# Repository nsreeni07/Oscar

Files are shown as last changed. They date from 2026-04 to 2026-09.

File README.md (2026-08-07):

OSCAR

Autonomous UAV system for precision agricultural crop monitoring

OSCAR is a custom-built 850mm quadcopter designed to fly automated survey missions over farmland and produce NDVI (Normalized Difference Vegetation Index) health maps of crops. It flies pre-programmed waypoint missions on INAV, captures geotagged near-infrared imagery, and a ground station does orthomosaic stitching and vegetation analysis. The end result is a color-coded map of a field showing where crops are healthy, where they're under irrigation stress, and where disease pressure might be building, all without a human piloting the aircraft or walking the field.

Onshape CAD: https://cad.onshape.com/documents/19523291b70a9c787e4fbec5/w/8af018b0ace6f9250dc6f3df/e/06f56f02d452d38e7c73aa30 
Full BOM: https://docs.google.com/spreadsheets/d/1ItluG4JZ7m0poAZtw0F7x5zs6U-Jy8w3EoTn_GnxS2I

How it works

OSCAR flies a field, takes pictures, and turns those pictures into a crop health map. Three steps:

Plan — a survey area is broken into a grid of GPS waypoints with enough overlap for the images to stitch together later. This mission gets loaded onto the flight controller in INAV Configurator.
Fly and capture — the drone flies the waypoints on its own. At each one, the flight controller tells the Pi Zero 2W over MAVLink that it's arrived. The Pi triggers the NIR camera  and geotags the image with the GPS position.
Process — after landing, the images go from the Pi's SD card to a ground station laptop running WebODM. WebODM stitches them into one map of the field and runs NDVI, which compares red vs. near-infrared reflectance to score plant health. Healthy plants reflect a lot of NIR, stressed or dying plants reflect more red. WebODM turns that into a color map, red for poor health, green for good, so problem spots in the field are obvious at a glance.







# Project OSCAR — Bill of Materials
|OSCAR — Updated Bill of Materials|FIELD2 |FIELD3|FIELD4 |FIELD5 |FIELD6 |FIELD7 |
|---|---|---|---|---|---|---|
| | | | | | | |
|Category |Item |Qty |Unit Price ($)|Line Total ($)|Notes |Link |
|Flight Controller / ESC |SpeedyBee F405 V4 BLS 60A 30x30 FC + 60A 4-in-1 ESC|1 |$70.31 |$70.31 |FC + ESC stack, replaces F722 + separate PDB/PM06 |https://tinyurl.com/2nz8ucyx |
|Companion Computer |Raspberry Pi Zero 2W |1 |$20.00 |$20.00 |Runs NDVI pipeline + MAVLink telemetry |https://www.adafruit.com/piz2w?src=raspberrypi |
|Camera |Pi Camera v2 NoIR |1 |$15.00 |$15.00 |Paired with 680nm bandpass filter for NDVI |https://www.pishop.us/product/raspberry-pi-noir-camera-module-v2/?src=raspberrypi|
|Power |XT90 Male-Female Pairs |1 |$3.00 |$3.00 |Battery-to-frame power connectors |https://tinyurl.com/m3hn7ykb |
|Power Protection |50V 2200µF Low-ESR Electrolytic Capacitor |1 |$3.00 |$3.00 |Across ESC battery pads — 6S voltage spike protection|https://tinyurl.com/yksjk3cu |
|Logistics |Shipping |1 |$35.00 |$35.00 |Combined shipping across vendors | |
| | | |Total |$146.31 | | 

Assembly

Build order, roughly in this sequence:

Frame — Cut the four CF tubes to 500mm. Press heat-set inserts into the 3D printed motor mount clamps, bolt clamps onto the tube ends. Assemble the central hub, routing motor and GPS/telemetry wiring through it before closing it up. Leave the FC/ESC deck plate off for now.

Propulsion — Bolt on the motors with threadlocker on every screw. Hold off on props until after ESC calibration. Two props are CW, two are CCW, check rotation direction against the SpeedyBee's motor order before mounting.

Power wiring — Solder the XT60 to the main 12 AWG battery leads, then wire the 4-in-1 ESC to the same leads. Solder the 2200uF capacitor across the ESC's battery pads for spike protection. Run 18 AWG phase wire from each motor through the arm tubes to its ESC output. Wire the two UBECs off the main power lead, one to the FC, one to the Pi, kept separate.
Flight controller — Mount the SpeedyBee F405 V4 stack on its vibration grommets near the frame's center of mass. Mount the GPS/compass on a mast, away from the ESC. Wire the SiK telemetry radio to a UART. Bind and wire the FlySky receiver to iBus.

Flash and configure INAV — Flash INAV to the SpeedyBee. Set the mixer to quad X, calibrate accelerometer and compass, confirm GPS lock, run ESC calibration with props off, set RC failsafe to RTL. Only mount props after confirming motor direction and throttle response in the motor test tab.

Payload — Confirm the IR-cut filter is removed from the NoIR camera, then thread on the 680nm bandpass filter. Connect the camera to the Pi Zero 2W via the CSI adapter. Mount the Pi and camera on the passive gimbal, mount the gimbal to the frame's underside. Power the Pi off its own UBEC rail.

Telemetry link and trigger logic — Wire a UART from the flight controller to the Pi so it can read the MAVLink stream. Run the waypoint-reached listener script from UAV Code/ on the Pi, which fires the camera and geotags on trigger. Bench-test this indoors before flying.

Balance and pre-flight check — Confirm the aircraft balances near center with the battery installed, arms are square, and motors spin freely. Run a full pre-flight (GPS lock, compass, RC link, telemetry link) and a hover test before attempting a waypoint mission.

Ground station — Install WebODM . After a flight, pull images off the Pi's SD card, load them into a WebODM project, and run the orthomosaic and NDVI task. Output is viewable in WebODM or exportable as a GeoTIFF.|

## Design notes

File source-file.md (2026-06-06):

https://cad.onshape.com/documents/ae291fcf005e21f8ead63777/w/105ae2836a2d5d7bdb4a4c74/e/ae3124f8bb89971ef9b9c9ca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

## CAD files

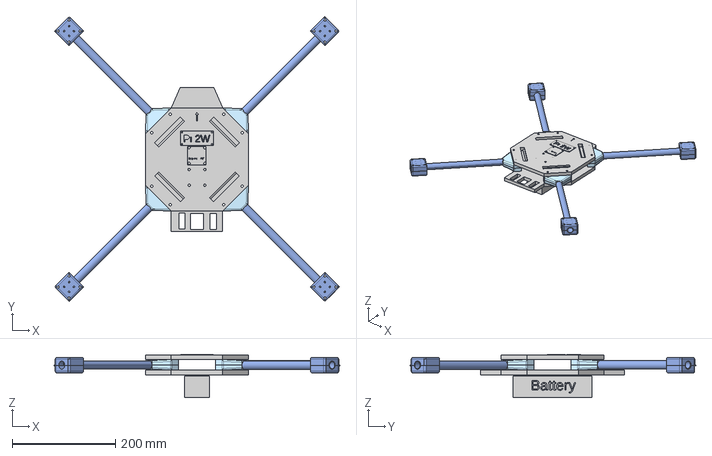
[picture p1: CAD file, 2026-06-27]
CAD Models/Oscar Drone Full Model with Electronics.step
553.1 x 553.1 x 83.9 mm

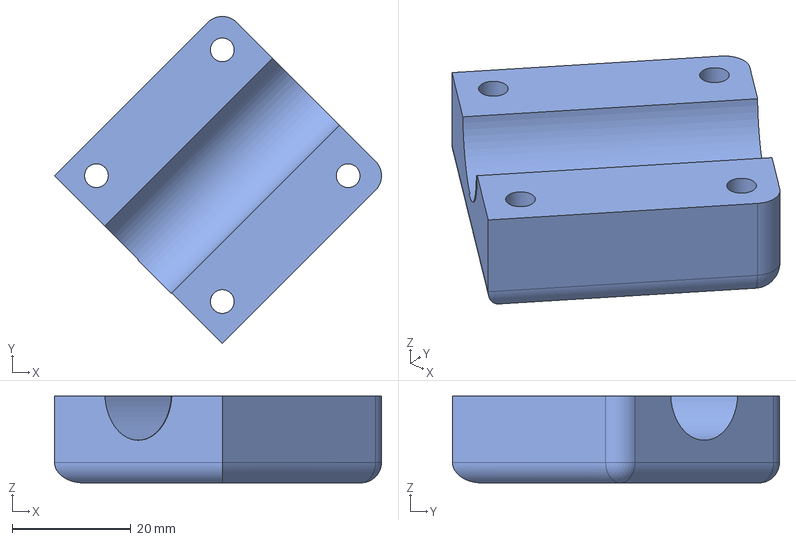
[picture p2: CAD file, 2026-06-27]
CAD Models/Part Studio 1 - Motor Mount Botto FR.step
55.1 x 55.1 x 14.7 mm

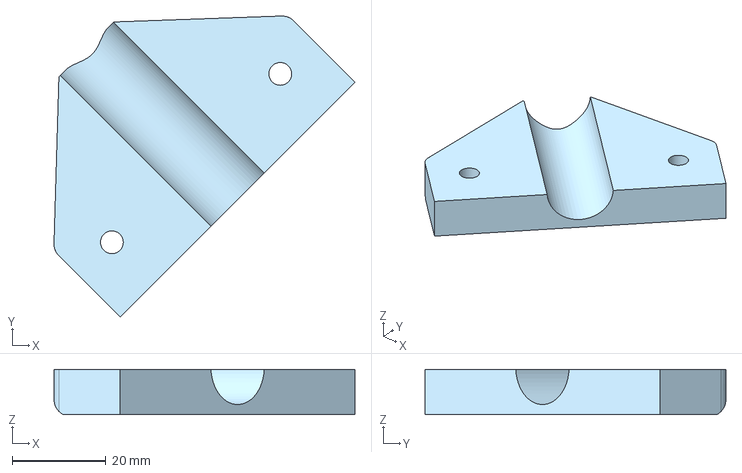
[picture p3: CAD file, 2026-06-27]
CAD Models/Part Studio 1 - Arm Mount FL 2.step
64.1 x 64.1 x 9.65 mm

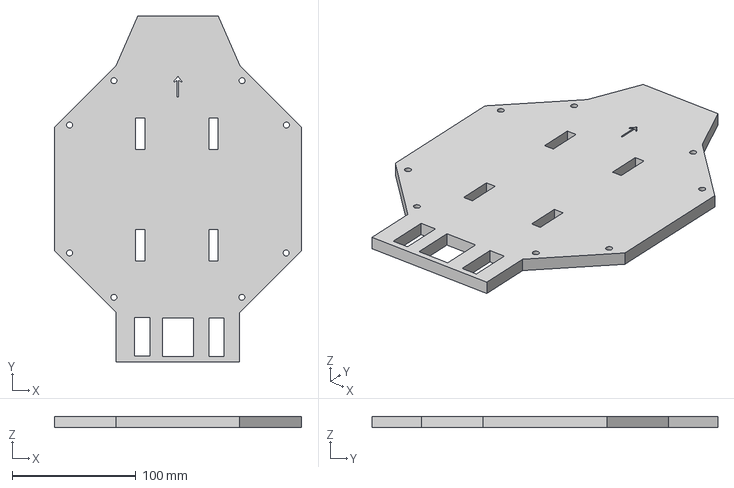
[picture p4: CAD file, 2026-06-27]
CAD Models/Part Studio 1 - Bottom Plate (1).step
200.2 x 280.0 x 9.00 mm

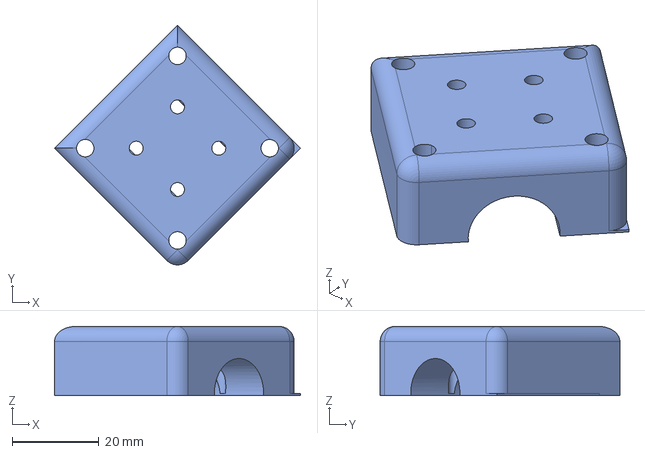
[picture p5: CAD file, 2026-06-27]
CAD Models/Part Studio 1 - Motor Mount Top RR.step
56.6 x 55.1 x 15.9 mm

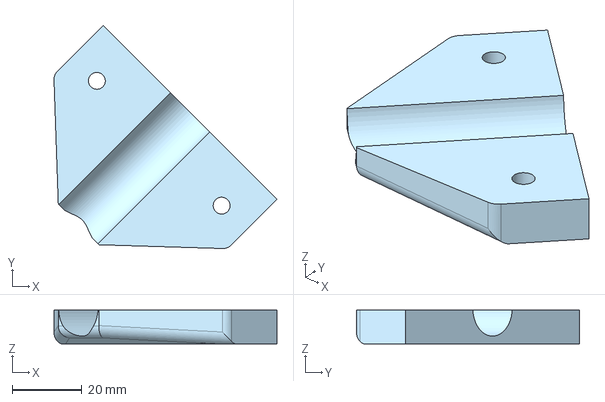
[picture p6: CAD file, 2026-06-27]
CAD Models/Part Studio 1 - Arm Mount RL 2.step
64.1 x 64.1 x 9.65 mm

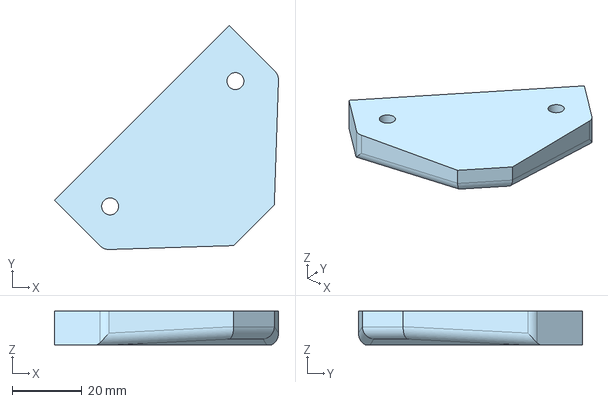
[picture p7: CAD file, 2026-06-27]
CAD Models/Part Studio 1 - Arm Mount RR 2.step
64.1 x 64.1 x 9.65 mm

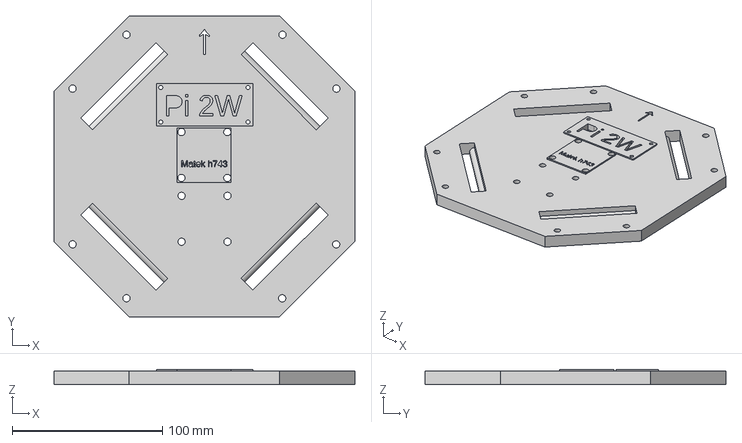
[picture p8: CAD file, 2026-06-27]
CAD Models/Part Studio 1 - Top Plate.step
200.2 x 200.0 x 10.0 mm

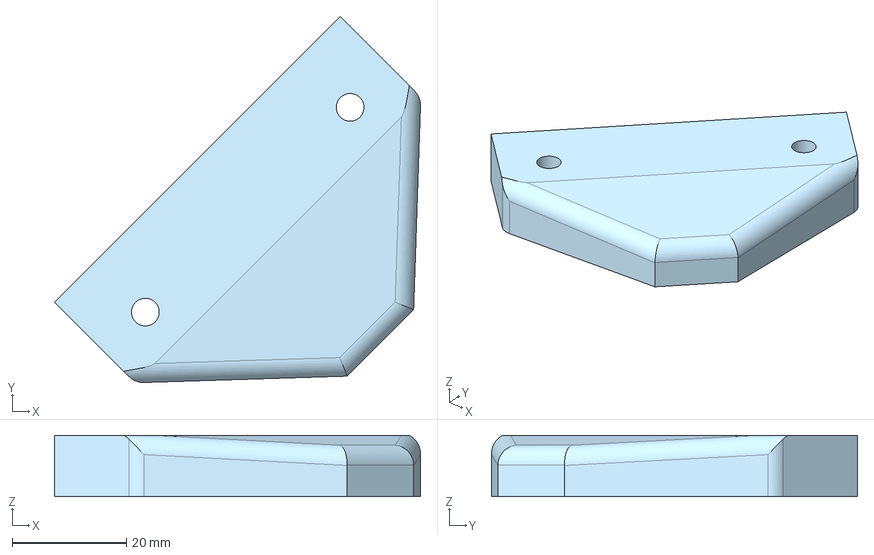
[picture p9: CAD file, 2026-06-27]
CAD Models/Part Studio 1 - Arm Mount RR 1.step
64.1 x 64.1 x 10.7 mm

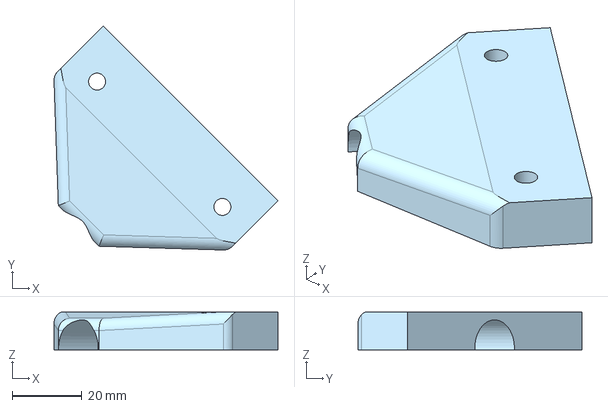
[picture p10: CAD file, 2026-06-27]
CAD Models/Part Studio 1 - Arm Mount RL 1.step
64.1 x 64.1 x 10.7 mm

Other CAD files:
CAD Models/Part Studio 1 - Motor Mount Bottom RL.step
CAD Models/Part Studio 1 - Motor Mount Top FR.step
CAD Models/Part Studio 1 - Arm Mount FR 2.step
CAD Models/Part Studio 1 - Motor Mount Top RL.step
CAD Models/Part Studio 1 - Motor Mount Bottom RR.step
CAD Models/Part Studio 1 - Motor Mount Top FL.step
CAD Models/Part Studio 1 - Arm Mount FR 1.step
CAD Models/Part Studio 1 - Arm Mount FL 1.step
CAD Models/Oscar Drone.step
CAD Models/Part Studio 1 - Motor Mount Bottom FR.step

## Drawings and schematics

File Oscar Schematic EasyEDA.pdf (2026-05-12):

## PDB

UBEC | +6V

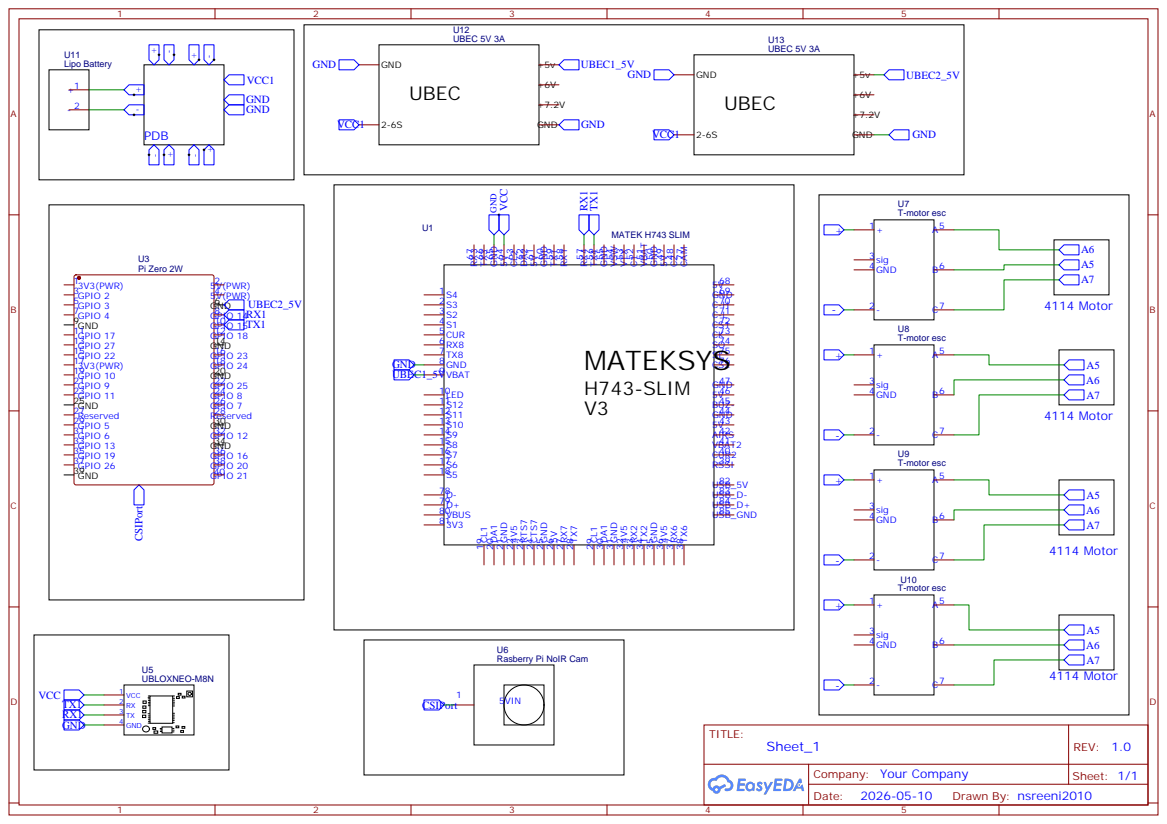
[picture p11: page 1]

Rasberry Pi NoIR Cam

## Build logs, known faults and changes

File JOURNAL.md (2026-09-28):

---
title: "OSCAR - Autonomous NDVI Agricultural Mapping Drone"
author: "nsreeni07"
description: "An 850mm quadcopter designed for autonomous NDVI agricultural mapping using a Raspberry Pi Zero 2W imaging payload and custom carbon fiber frame."
created_at: "2026-04-05"

---

# September 25: Thrust Calculations 

## Mass Budget

| Component | Mass |
|---|---|
| Frame (CF tubes, plates, hardware) | 380 g |
| Motors × 4 (4114 320KV, ~120 g each) | 480 g |
| Props × 4 (17-in CF, ~25 g each) | 100 g |
| SpeedyBee F405 V4 stack | 65 g |
| 6S 5000 mAh LiPo | 780 g |
| M8N GPS + compass | 28 g |
| SiK 915 MHz telemetry (air unit) | 25 g |
| FlySky FS-iA6B receiver | 16 g |
| Raspberry Pi Zero 2W | 23 g |
| Pi Camera v2 NoIR + 680 nm filter | 12 g |
| Passive gimbal assembly | 55 g |
| Wiring harness + connectors | 60 g |
| Misc hardware (standoffs, screws) | 40 g |
| **Subtotal** | **2,064 g** |
| **+ 5% build tolerance** | **2,167 g** |

---

## Thrust Analysis

| Parameter | Value |
|---|---|
| Motor | Tarot 4114 320KV |
| Prop | 17-in carbon fiber |
| Battery | 6S · 22.2 V nominal · 25.2 V full |
| No-load max RPM (22 V) | ~7,100 RPM |
| Max thrust per motor | 2,050 g (20.1 N) |
| Max thrust total (4×) | 8,200 g (80.4 N) |
| **Thrust-to-weight ratio** | **3.78 : 1** |
| Hover thrust required per motor | ~542 g |
| Hover throttle (estimated) | ~51% |


**Total time spent: 2 hours**

---

# April 5: Project Research and Initial BOM

Initially, I was planning to use the Pixhawk flight controller, however, its cost was very high, hence I had to start comparing flight controllers F4, F7, and H7 with respect to performance, cost and INAV compatibility. Autonomous waypoint navigation being an important part of this project, I further reduced the choices of controllers to F4 and F405 through comparison of characteristics such as UARTs, internal barometers and current sensors. The chosen batteries will be 4S LiPo and 14 AWG wire size. In order to keep track of my budget.
Initial BOM Draft

**Total time spent: 2 hours**

---

# April 6: System Architecture and Component Research

Today I was busy with system architecture design of OSCAR. The drone will fly according to predefined waypoints, capturing geotagged images that can be later stitched into orthomosaics and turned into NDVI maps for identifying crop health and stress. I decided to use Raspberry Pi Zero 2W with NoIR camera and 680 nm bandpass filter. In the course of my work, I discovered that Raspberry Pi has to wait for the MAVLink heartbeat before it starts receiving data from GPS module, which will be a useful part of the software initialization process. Besides, I have updated my bill of materials the total cost is currently about $200 without the frame and a few other elements.

System Architecture Diagram

**Total time spent: 2 hours**

---

# April 7: NDVI Processing Algorithm

As the hardware had not yet arrived, my attention was paid to software pipeline development for NDVI image processing to have everything ready before flight testing. because there is no multispectral data could be gathered from a NoIR camera with a 680 nm bandpass filter, an approximate NDVI algorithm using red and blue channels as substitutes for the red and near-infrared bands. Also in order to avoid a division by zero error, I added epsilon to the denominator and adjusted for the variable lighting conditions using per-image normalization.  The initial testing with "aerial images" of crops gave very good results

NDVI Algorithm Output 1
NDVI Algorithm Output 2

**Total time spent: 3 hours**

---

# April 8: Waypoint-Based Photo Capture Code and MAVLink Integration

This is where I have been able to make a huge upgrade to the image capture system of the drone because instead of the previous time-based system, I used the distance-based system that uses the Haversine formula. While the time-based system was capturing photos every two seconds, the new system calculates the distance moved since the last capture point based on the GPS coordinate and captures an image every 5 meters. This is irrespective of the change in the speed of the flight. I have been able to develop the MAVLink communication system using pymavlink that captures GLOBAL_POSITION_INT message when a heart beat from the flight controller is obtained.

Waypoint Capture Code
Waypoint Capture Code

**Total time spent: 2 hours**

---

# April 10: Wiring Diagram, BOM Update, and Camera Mount Design
I finished drawing up the wiring diagram which demonstrates connections between each of the main components such as the battery, power distribution board, ESCs, motors, flight controller, GPS, receiver and Raspberry Pi, and I noted the points where the bullet connectors and heat shrink tubing will be placed in order to make it easier to assemble the components without errors. Also, I finished designing the camera mount, and decided to use a stationary one instead of the gimbal due to extra cost.

Wiring Diagram

**Total time spent: 3 hours**

---

# April 11: MAVLink Integration and Camera Mount CAD

The next step in my MAVLink communication system within VS Code was to add the ability to detect heartbeats along with a timeout mechanism, read GPS information constantly from `GLOBAL_POSITION_INT`, read battery voltage from `SYS_STATUS`, and log raw messages for troubleshooting purposes. In addition, I created documentation for the whole hardware set-up, including UART configuration, baud rate setting at 115200, and `pymavlink` connection parameters. I finished the design for the Onshape CAD model for the camera mount, which includes a two-piece housing that features M3 stand-offs for mounting, 680 nm filter retaining lips, and vibration damping foam mounts. The fixed mount is a cheaper solution than the gimbal but works for slow agricultural mapping flights.

Camera Mount CAD

**Total time spent: 2 hours**

---

# April 13: Project Feedback and Redesign

From the feedback I got, the project should be made to have a more engineering approach since most of the work in the original design had been based on buying and assembling. I modified my design of OSCAR so that the target will still remain autonomous NDVI agricultural mapping. In the new design, there will be a 850 mm carbon fiber drone frame from scratch and maybe develop a custom flight controller. 

[Updated Project Doc](https://docs.google.com/document/d/19ZpP3lER7y1khA4oXiPfYRFo_DdoW_JR/edit)

OSCAR Project Dossier

**Total time spent: 1 hour**

---

# April 20: Custom Frame Design and Sponsorship Outreach

I began designing the custom 850 mm drone frame by researching existing large drone designs to understand common structural approaches, including motor spacing, plate thickness, and arm configurations. I then started modeling the bottom plate in Onshape with a 30 × 30 mm M3 mounting pattern for the F722 flight controller and integrated battery strap slots. I also rethought the project budget and created a funding plan where a $100 of personal contribution, and $200 from Stasis funding, and another $200 through external sponsors. I alsp began making a list of potential sponsors and drafting outreach emails to companies in the drone and precision agriculture industries.

Frame Bottom Plate CAD

**Total time spent: 4 hours**

---

# April 26: CAD Model Revamp and Updated Dossier

My main concern was to make the organization of my Onshape assembly by bringing together all the previous files, which had been separated and also correcting all the mates of the plates, arms, and all other components. The basic geometry of the whole frame is almost done except for the motor mount, which I need to bring in from another file. In my current design, I used a 4 mm bottom plate, a 3 mm top plate, and 15 × 15 mm square arm tubes. As I am going to use 3D printed PETG in place of carbon fiber in my prototype, I made the plate thicker for extra support.

Full CAD Model

**Total time spent: 2 hours**

---

# May 5: Final CAD and Budget Finalized

The design is all set, and the test fit looks great. Motor bolts line up, the flight controller stack fits fine, the camera has a clear view straight down, and the battery sits right on the center of gravity. Wiring works as-is, but adding dedicated internal cable channels in the future would definitely clean things up.

Total cost landed right around $650, mostly driven by the motors, props, stack, battery, and camera setup.

Final CAD Assembly

**Total time spent: 2 hours**

---

# May 7: CAD Fixes and Pitch Refresh
I worked on designing the motor mounts where I modified the size of heat set insert holes to allow for a better fit into PETG material. I reduced the hole size from 5.0 mm to 4.85 mm which is 0.15 mm undersized. This allows the heat set insert to embed itself into the plastic when it melts. I also worked on modifying my project pitch to make the problem more apparent. I also worked on the cost aspect of having professional NDVI mapping drones for small farms and students.

CAD Holes Update

**Total time spent: 0.4 hour**

---

# June 6: Flight Controller Switch and Capacitor
I replaced the F722 flight controller with the SpeedyBee F405 V4 stack, which has the flight controller and 60A 4-in-1 BLS ESC in one more compact and less expensive set. It lowers costs, gets rid of soldering needed between the FC and ESC. The stack still works with my old FlySky i6 transmitter and FS-iA6B receiver via iBUS, and the 60A ESC is quite enough for my motors, which are estimated to consume 25-30A at full throttle. I decided to add a 50V 2200 µF low-ESR electrolytic capacitor to the system in order to save the power system from any possible voltage spikes related to the fast change of the current used by the motors.

Speedybee F405 V4

**Total time spent: 1 hour**

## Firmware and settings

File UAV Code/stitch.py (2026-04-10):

import cv2
import os
import sys
import math

# -----------------------------
# SETTINGS
# -----------------------------
IMAGE_FOLDER = "captured_images"   # Folder of drone images
OUTPUT_FILE  = "stitched_output.jpg"
MAX_IMAGES   = 50                  # Cap per stitch pass (RAM safety)
RESIZE_WIDTH = 1920                # Downscale before stitching (faster, less RAM)

# -----------------------------
# LOAD IMAGES
# Sorted by filename = sorted by capture order (our filenames include count + timestamp)
# -----------------------------
def load_images(folder, max_count=MAX_IMAGES):
    supported = (".jpg", ".jpeg", ".png")
    files = sorted([
        f for f in os.listdir(folder)
        if f.lower().endswith(supported)
    ])

    if not files:
        print(f"No images found in '{folder}'")
        sys.exit(1)

    if len(files) > max_count:
        print(f"Found {len(files)} images — capping at {max_count} for RAM safety.")
        print(f"For full mosaics, run in batches or use WebODM.")
        files = files[:max_count]

    images = []
    for fname in files:
        path = os.path.join(folder, fname)
        img = cv2.imread(path)
        if img is None:
            print(f"  Warning: could not read {fname}, skipping")
            continue

        # Downscale to RESIZE_WIDTH to keep RAM usage reasonable
        h, w = img.shape[:2]
        if w > RESIZE_WIDTH:
            scale = RESIZE_WIDTH / w
            img = cv2.resize(img, (RESIZE_WIDTH, int(h * scale)))

        images.append(img)
        print(f"  Loaded: {fname} ({img.shape[1]}x{img.shape[0]})")

    return images

# -----------------------------
# STITCH
# -----------------------------
def stitch_images(images):
    print(f"\nAttempting to stitch {len(images)} images...")

    # SCANS mode is more robust for aerial/overlapping imagery than PANORAMA
    stitcher = cv2.Stitcher_create(cv2.Stitcher_SCANS)

    status, stitched = stitcher.stitch(images)

    if status == cv2.Stitcher_OK:
        cv2.imwrite(OUTPUT_FILE, stitched, [cv2.IMWRITE_JPEG_QUALITY, 95])
        h, w = stitched.shape[:2]
        size_mb = os.path.getsize(OUTPUT_FILE) / (1024 * 1024)
        print(f"\nStitching successful!")
        print(f"  Output: {OUTPUT_FILE}")
        print(f"  Size:   {w}x{h} pixels  ({size_mb:.1f} MB)")
        return True

    # Descriptive error codes
    errors = {
        cv2.Stitcher_ERR_NEED_MORE_IMGS:    "Not enough matching features between images. Try more overlap (fly slower / closer spacing).",
        cv2.Stitcher_ERR_HOMOGRAPHY_EST_FAIL: "Homography failed. Images may be too similar (low texture) or too far apart.",
        cv2.Stitcher_ERR_CAMERA_PARAMS_ADJUST_FAIL: "Camera parameter adjustment failed. Try fewer images or more overlap.",
    }
    reason = errors.get(status, f"Unknown error code {status}")
    print(f"\nStitching failed. {reason}")
    print("Stitching failed Brochacho lock in :(")
    return False

# -----------------------------
# MAIN
# -----------------------------
if __name__ == "__main__":
    # Optional: pass folder as argument
    if len(sys.argv) > 1:
        IMAGE_FOLDER = sys.argv[1]

    print(f"Loading images from: {IMAGE_FOLDER}")
    images = load_images(IMAGE_FOLDER)
    print(f"\nLoaded {len(images)} images successfully")

    success = stitch_images(images)

    if not success:
        print("\nTip: For 100+ drone images, use WebODM (free) for better results:")
        print("     https://webodm.net")

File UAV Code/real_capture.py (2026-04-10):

from pymavlink import mavutil
import math
import time

# -----------------------------
# SETTINGS
# -----------------------------
CAPTURE_DISTANCE = 5        # meters
MIN_CAPTURE_INTERVAL = 0.8  # seconds (GPS jitter guard)

# -----------------------------
# DISTANCE FUNCTION (Haversine)
# -----------------------------
def get_distance(lat1, lon1, lat2, lon2):
    R = 6371000
    phi1 = math.radians(lat1)
    phi2 = math.radians(lat2)
    dphi = math.radians(lat2 - lat1)
    dlambda = math.radians(lon2 - lon1)
    a = math.sin(dphi/2)**2 + math.cos(phi1)*math.cos(phi2)*math.sin(dlambda/2)**2
    c = 2 * math.atan2(math.sqrt(a), math.sqrt(1-a))
    return R * c

# -----------------------------
# CONNECT
# -----------------------------
print("Connecting to flight controller...")
master = mavutil.mavlink_connection('COM3', baud=115200)
master.wait_heartbeat()
print("Connected!")

last_position = None
last_capture_time = 0

# -----------------------------
# MAIN LOOP
# -----------------------------
while True:
    msg = master.recv_match(type='GLOBAL_POSITION_INT', blocking=True)

    if msg is not None:
        lat = msg.lat / 1e7
        lon = msg.lon / 1e7
        alt = msg.alt / 1000.0

        print(f"GPS: {lat:.6f}, {lon:.6f}  Alt: {alt:.1f}m")

        if last_position is not None:
            dist = get_distance(last_position[0], last_position[1], lat, lon)
            now = time.time()
            print(f"Moved: {dist:.2f}m")

            if dist >= CAPTURE_DISTANCE and (now - last_capture_time) >= MIN_CAPTURE_INTERVAL:
                print("TAKE PHOTO")
                # TODO: Replace with real camera trigger
                # capture_image()
                last_capture_time = now

        # Always update — not just on capture
        last_position = (lat, lon)

    time.sleep(0.1)

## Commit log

2026-04-07 Create Camera Trigger
2026-04-10 Update Camera Trigger
2026-06-07 Revise journal entries for CAD and flight controller
    Updated journal entries with recent changes to CAD and BOM.
2026-06-27 Rename Oscar Drone.step to CAD Models/Oscar Drone.step
    [Oscar Drone.step]
2026-06-27 Add links to items in the Bill of Materials
    Updated the Bill of Materials to include links for each item.
2026-06-27 Update README with Onshape link
    Added Onshape link for CAD documentation.
2026-06-27 Revise OSCAR BOM with updated items and totals
    Updated the Bill of Materials with new entries and total cost.
    [OSCAR BOM Final V7.csv]
2026-06-27 Update BOM link in README.md
2026-06-27 Update README with Onshape and BOM links
    Added links to Onshape and BOM for reference.
2026-06-27 Update Bill of Materials title in README
